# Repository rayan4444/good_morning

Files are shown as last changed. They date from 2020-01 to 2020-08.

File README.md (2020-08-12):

# Curtain scheduler

Scheduled curtain control: opens and closes at specific times

# Mechanical
### Assets
* Fusion 360 link: https://a360.co/35GVD2y
* See release for STEP/STL files

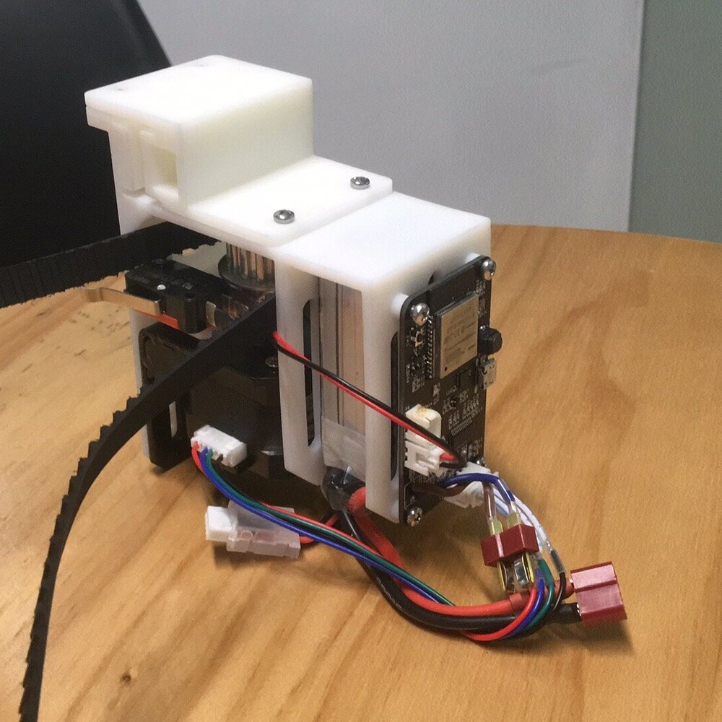
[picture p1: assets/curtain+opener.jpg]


### Improvements
* Add stiffness/ribs to reduce outer frame deflection
* smaller PCB mounting holes (changed diametr from 3mm to 2.7mm)
* larger chamfer to match curtain rail I have at home
* tighter tolerance on bearing holder
* choose a lighter/smaller motor bracket
* choos weaker/smaller mechanical end stops

# Electronics

### Description
Features:
* ESP32 WROOM32 module
* 1x button
* 1x programmable LED
* 1x VEML6030 ambient light sensor
* 1x CP2104 USB-UART bridge
* 1x DRV8825 stepper motor driver with controllable STEP, DIR, /SLEEP and /ENA

Power:
* 3S Lipo battery, charged externally - not by this board
* LDO for USB power during programming
* 12V-3.3V 1A switching regulator
* resistor divider to monitor battery voltage

>find out how long it lasts on 1 full charge

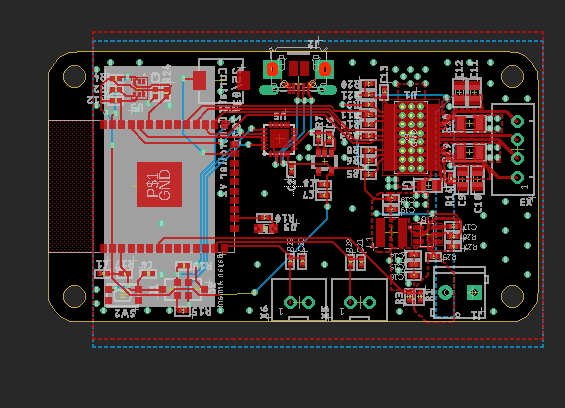
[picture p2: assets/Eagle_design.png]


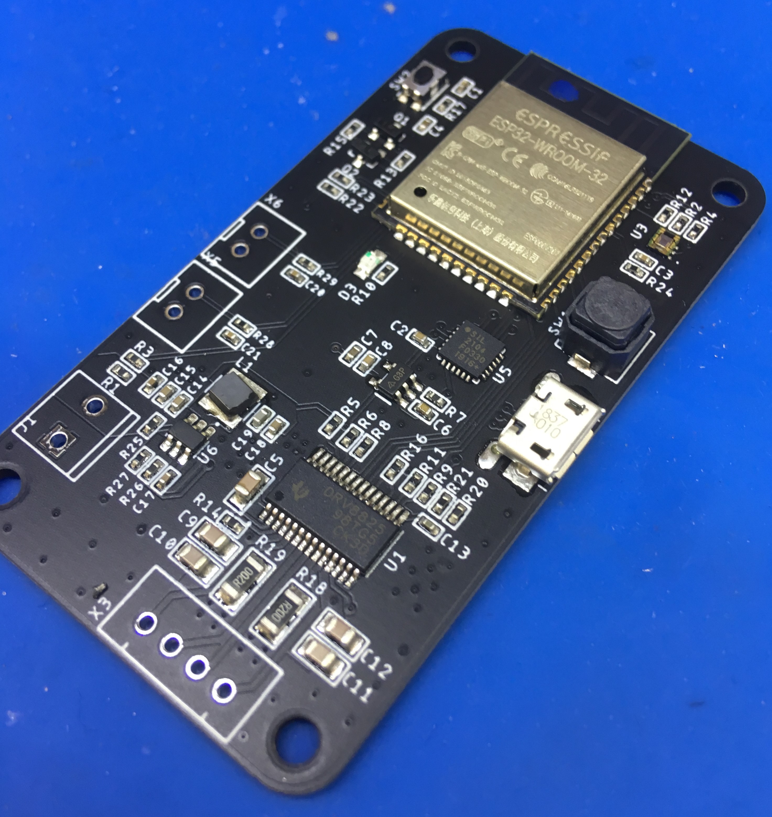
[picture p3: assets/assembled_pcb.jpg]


### Pinout
|Signal|Pin|Notes|
|:---:|:----:|:---:|
|Stepper_step|16||
|Stepper_direction|17||
|Stepper_enable|4|active low|
|Stepper_sleep|5|active low|
|Limit_switch_1|14|has external pullup (R23)|
|Limit_switch_2|12|no external pullup (R22), enable internal pullup|
|I2C_SCL|22||
|I2C_SDA|23||
|Ambient_light_sensor_int|21||
|LED|13||
|Button|15|enable internal pullup|
|Battery_voltage|I35, A1_7|ADC1 channel 7|

### Errata
* Remove R22: the external pullup messes with communication with flash when programming.
* Add 10k pull up resistor on the nENA line so that when the MCU is asleep the stepper is not enabled.

# Firmware

### Structure
* Wake up from sleep
* configure pins
* check battery level: if it is low blink the light and get stuck in this mode until the battery is recharged
* else, connect to wifi
* get time from NTP server
* check if it time to open/close the curtains
* open/close the curtains
* turn Wi-Fi OFF
* set wake up timer
* set wake up button
* go into deep sleep

> NOTE: this firmware version doesn't use the end stops to check the curtain status because the end stops I have are too strong and don't work. It will be updated once I find new end stops.

### Personal notes / improvements to do
* have a seperate RTC chip with less drift ?
* you can retain some simple things in RTC memory
```cpp
RTC_DATA_ATTR int bootCount = 0;
```
* change open/close times over wifi (from M5 stack core maybe?)
* "wireless wake up"?
* gather data from ambient light sensor over a week or so and see if there are any interesting patterns

### Reference links
* [deep sleep](https://lastminuteengineers.com/esp32-deep-sleep-wakeup-sources/)
* [NTP server](https://lastminuteengineers.com/esp32-ntp-server-date-time-tutorial/)
* [stepper driving with timers]()

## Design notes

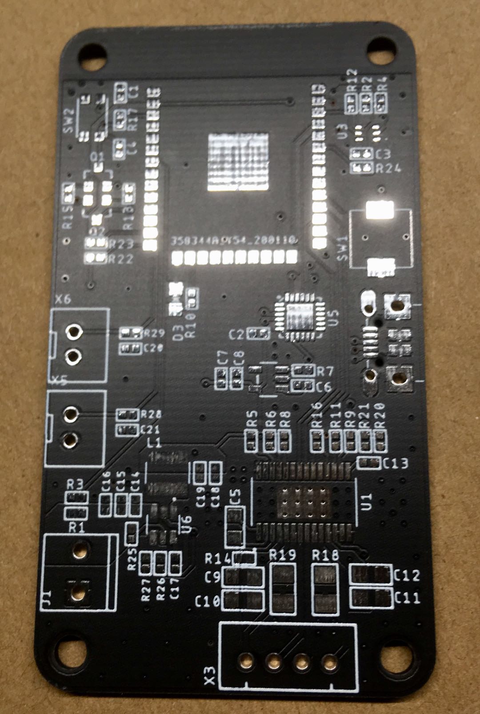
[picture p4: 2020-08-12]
assets/blank_pcb.jpg

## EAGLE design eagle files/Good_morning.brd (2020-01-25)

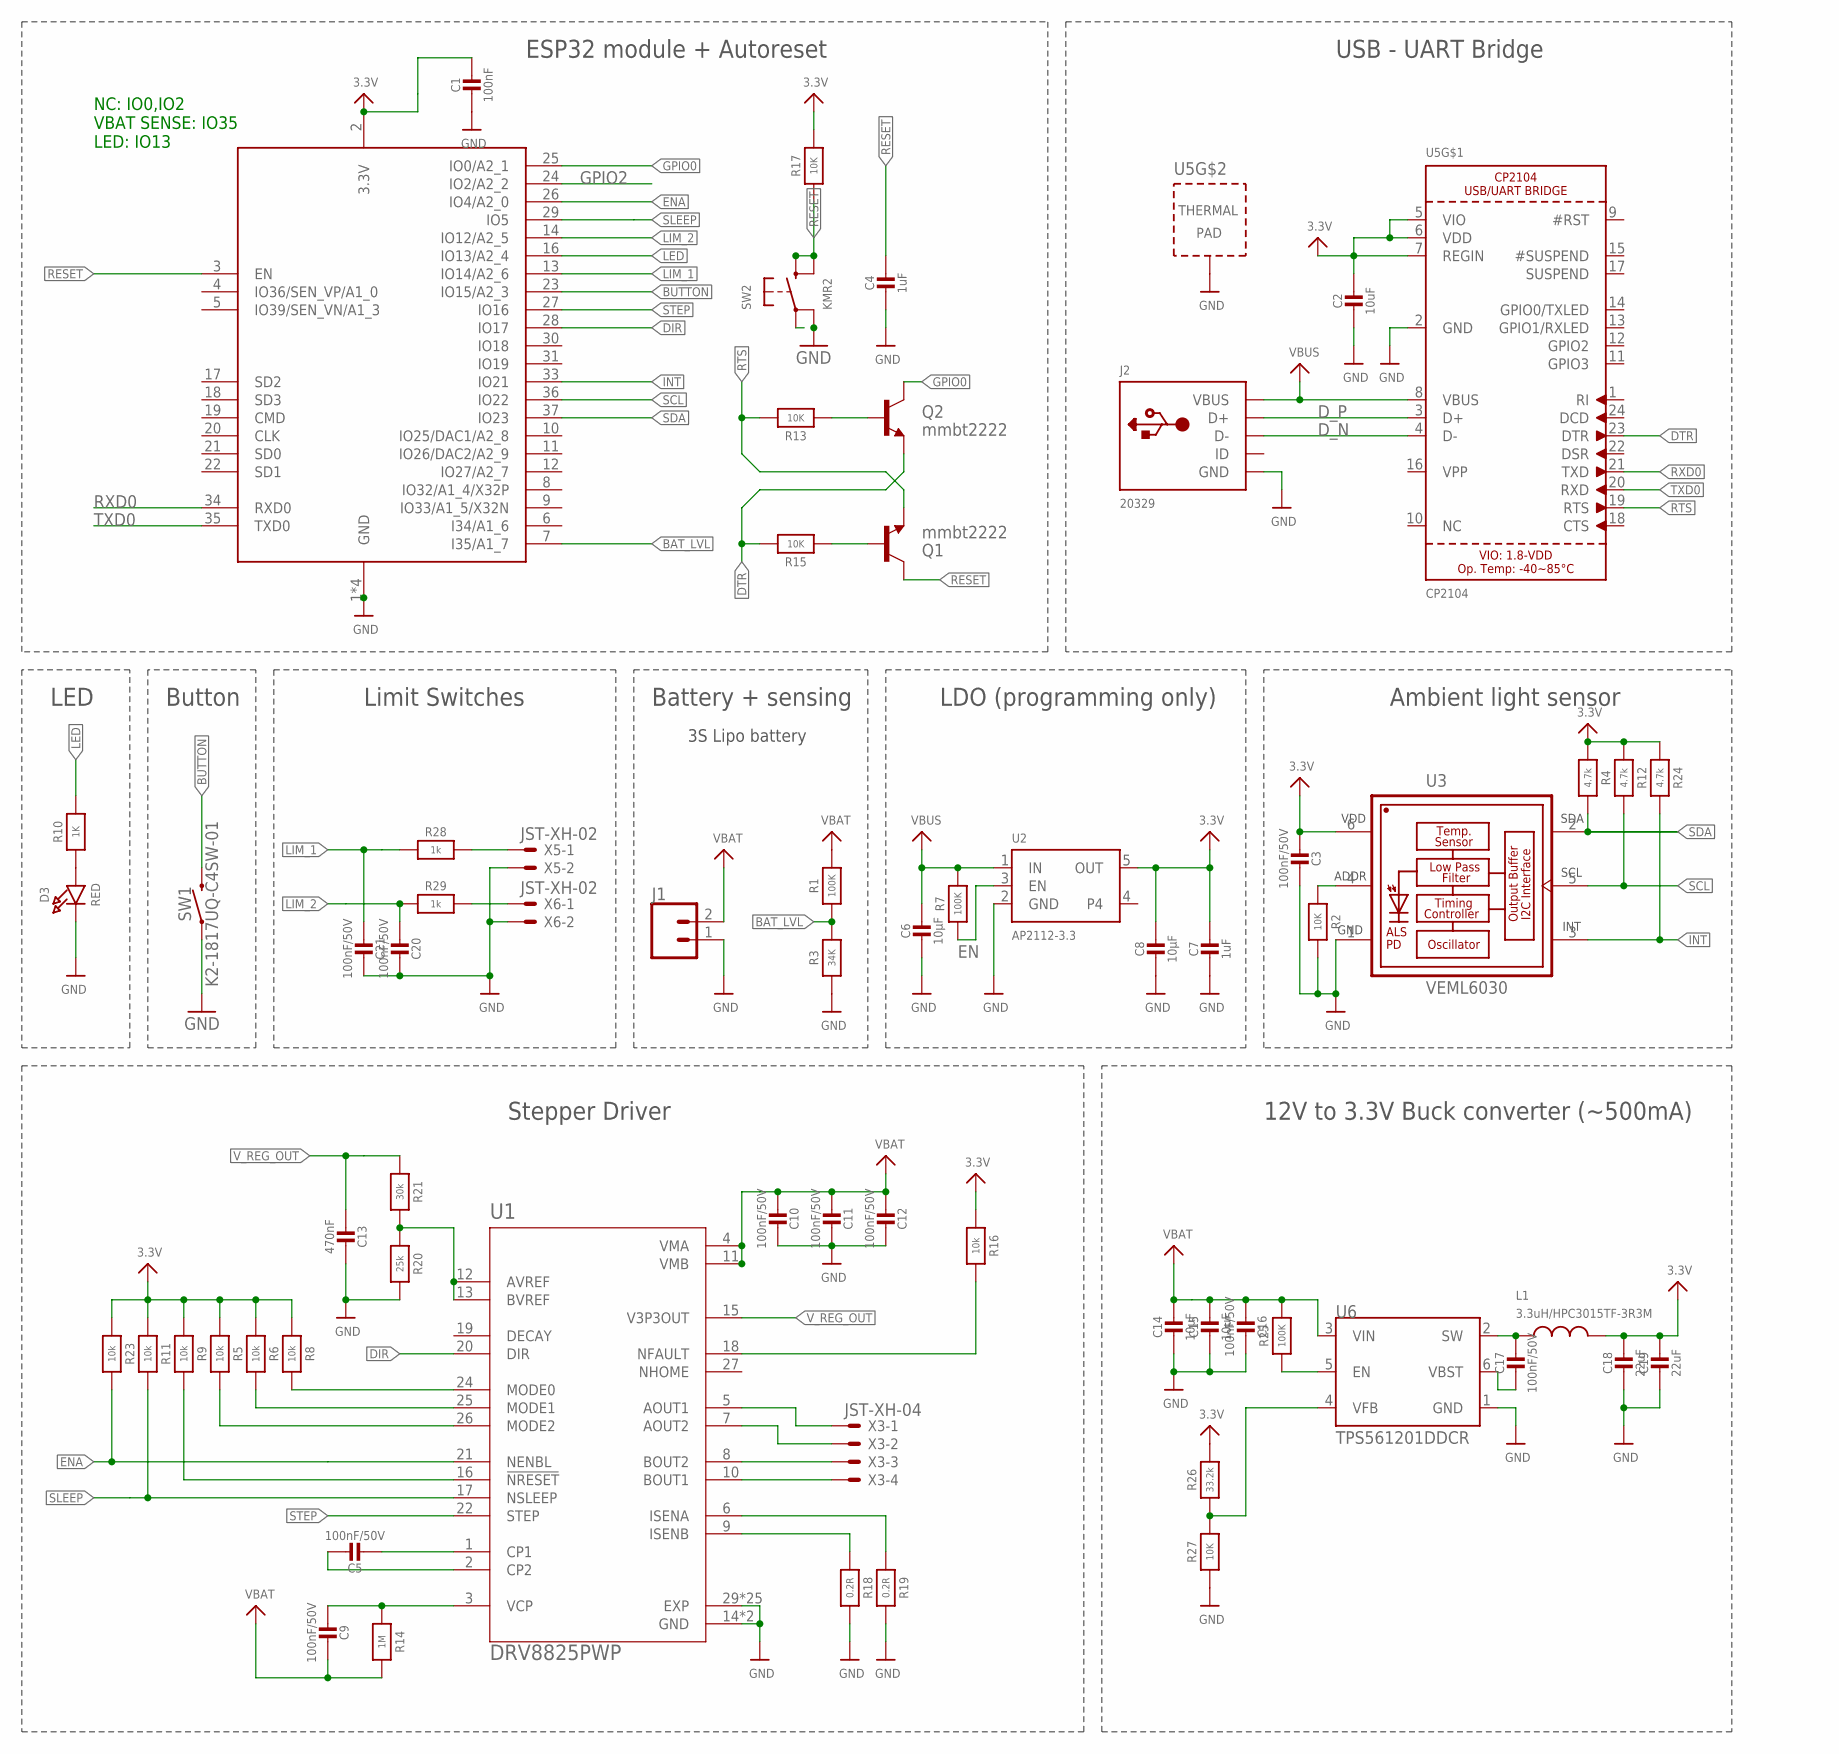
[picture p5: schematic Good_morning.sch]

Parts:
C1: 100nF; _0402
C2: 10uF; _0402
C3, C16, C17, C20, C21: 100nF/50V; _0402
C4, C7: 1uF; _0402
C5, C9, C10, C11, C12: 100nF/50V; _0805
C6, C8, C14, C15: 10µF; _0402
C13: 470nF; _0402
C18, C19: 22uF; _0402
D3: RED; CHIPLED_0805_NOOUTLINE
J1: CONN_023.5MM_LOCK; SCREWTERMINAL-3.5MM-2_LOCK
J2: 20329; 4UCONN_20329_V2
L1: 3.3uH/HPC3015TF-3R3M; WPN4020H100MT
Q1, Q2: mmbt2222; SOT23-3
R1, R7, R25: 100K; _0402
R2, R13, R15, R17, R27: 10K; _0402
R3: 34K; _0402
R4, R12, R24: 4.7k; _0402
R5, R6, R8, R9, R11, R16, R23: 10k; _0402
R10: 1K; _0402
R14: 1M; _0402
R18, R19: 0.2R; _1206
R20: 25k; _0402
R21: 30k; _0402
R26: 33.2k; _0402
R28, R29: 1k; _0402
SW1: K2-1817UQ-C4SW-01
SW2: KMR2; BTN_KMR2_4.6X2.8
U1: DRV8825PWP; SOP65P640X120-29N
U2: AP2112-3.3; SOT23-5
U3: VEML6030; VISHAY_VEML6030_2X2X0.87
U4: ESP32_WROOM32_SKINNY; WROOM32_SKINNY
U5: CP2104; QFN24_4MM_SMSC
U6: TPS561201DDCR; SOT95P280X110-6N
X3: JST-XH-04; JST-XH-04-PACKAGE-ROUND-PAD
X5, X6: JST-XH-02; JST-XH-02-PACKAGE-ROUND-PAD

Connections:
3.3V: C1.1, C2.1, C3.2, C7.1, C8.1, C18.1, C19.1, L1.2, R4.1, R5.1, R6.1, R8.1, R9.1, R11.1, R12.1, R16.1, R17.2, R23.1, R24.1, R26.1, U2.5 (OUT), U3.6 (VDD), U4.2 (3.3V), U5.5 (VIO), U5.6 (VDD), U5.7 (REGIN)
BAT_LVL: R1.1, R3.2, U4.7 (I35/A1_7)
BUTTON: SW1.P$2 (2), U4.23 (IO15/A2_3)
DIR: U1.20 (DIR), U4.28 (IO17)
DTR: Q2.2 (E), R15.2, U5.23 (DTR)
D_N: J2.D-, U5.4 (D-)
D_P: J2.D+, U5.3 (D+)
EN: R7.1, U2.3 (EN)
ENA: R23.2, U1.21 (NENBL), U4.26 (IO4/A2_0)
GND: C1.2, C2.2, C3.1, C4.2, C6.2, C7.2, C8.2, C10.1, C11.1, C12.1, C13.1, C14.2, C15.2, C16.1, C18.2, C19.2, C20.1, C21.1, D3.C, J1.1, J2.BASE@1 (GND), J2.BASE@2 (GND), J2.GND, J2.SPRT@1 (GND), J2.SPRT@2 (GND), J2.SPRT@3 (GND), J2.SPRT@4 (GND), R2.2, R3.1, R18.2, R19.2, R20.2, R27.1, SW1.P$1 (1), SW2.A' (P1), U1.14 (GND), U1.28 (GND), U1.29 (EXP), U1.P1 (EXP), U1.P2 (EXP), U1.P3 (EXP), U1.P4 (EXP), U1.P5 (EXP), U1.P6 (EXP), U1.P7 (EXP), U1.P8 (EXP), U1.P9 (EXP), U1.P10 (EXP), U1.P11 (EXP), U1.P12 (EXP), U1.P13 (EXP), U1.P14 (EXP), U1.P15 (EXP), U1.P16 (EXP), U1.P17 (EXP), U1.P18 (EXP), U1.P19 (EXP), U1.P20 (EXP), U1.P21 (EXP), U1.P22 (EXP), U1.P23 (EXP), U1.P24 (EXP), U2.2 (GND), U3.1 (GND), U4.1 (GND), U4.15 (GND), U4.38 (GND), U4.P$1 (GND), U5.2 (GND), U5.THERM (TP), U6.1 (GND), X5.2, X6.2
GPIO0: Q2.3 (C), U4.25 (IO0/A2_1)
GPIO2: U4.24 (IO2/A2_2)
INT: R24.2, U3.3 (INT), U4.33 (IO21)
LED: R10.1, U4.16 (IO13/A2_4)
LIM_1: C21.2, R28.1, U4.13 (IO14/A2_6)
LIM_2: C20.2, R29.1, U4.14 (IO12/A2_5)
unnamed: R2.1, U3.4 (ADDR)
unnamed: U1.8 (BOUT2), X3.3
unnamed: U1.10 (BOUT1), X3.4
unnamed: D3.A, R10.2
unnamed: R28.2, X5.1
unnamed: R25.1, U6.5 (EN)
unnamed: Q2.1 (B), R13.1
unnamed: R8.2, U1.24 (MODE0)
unnamed: R6.2, U1.25 (MODE1)
unnamed: R5.2, U1.26 (MODE2)
unnamed: Q1.1 (B), R15.1
unnamed: R9.2, U1.16 (!NRESET)
unnamed: C17.1, L1.1, U6.2 (SW)
unnamed: C5.2, U1.1 (CP1)
unnamed: C5.1, U1.2 (CP2)
unnamed: C9.2, R14.1, U1.3 (VCP)
unnamed: C17.2, U6.6 (VBST)
unnamed: R20.1, R21.2, U1.12 (AVREF), U1.13 (BVREF)
unnamed: R16.2, U1.18 (NFAULT)
unnamed: R29.2, X6.1
unnamed: U1.5 (AOUT1), X3.1
unnamed: U1.7 (AOUT2), X3.2
unnamed: R26.2, R27.2, U6.4 (VFB)
unnamed: R19.1, U1.6 (ISENA)
unnamed: R18.1, U1.9 (ISENB)
RESET: C4.1, Q1.3 (C), R17.1, SW2.B (S), SW2.B' (S1), U4.3 (EN)
RTS: Q1.2 (E), R13.2, U5.19 (RTS)
RXD0: U4.34 (RXD0), U5.21 (TXD)
SCL: R12.2, U3.5 (SCL), U4.36 (IO22)
SDA: R4.2, U3.2 (SDA), U4.37 (IO23)
SLEEP: R11.2, U1.17 (NSLEEP), U4.29 (IO5)
STEP: U1.22 (STEP), U4.27 (IO16)
TXD0: U4.35 (TXD0), U5.20 (RXD)
VBAT: C9.1, C10.2, C11.2, C12.2, C14.1, C15.1, C16.2, J1.2, R1.2, R14.2, R25.2, U1.4 (VMA), U1.11 (VMB), U6.3 (VIN)
VBUS: C6.1, J2.VBUS, R7.2, U2.1 (IN), U5.8 (VBUS)
V_REG_OUT: C13.2, R21.1, U1.15 (V3P3OUT)

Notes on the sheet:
NC: IO0,IO2 VBAT SENSE: IO35 LED: IO13
LDO (programming only)
Stepper Driver
LED
Button
ESP32 module + Autoreset
Battery + sensing
USB - UART Bridge
Limit Switches
3S Lipo battery
12V to 3.3V Buck converter (~500mA)
Ambient light sensor

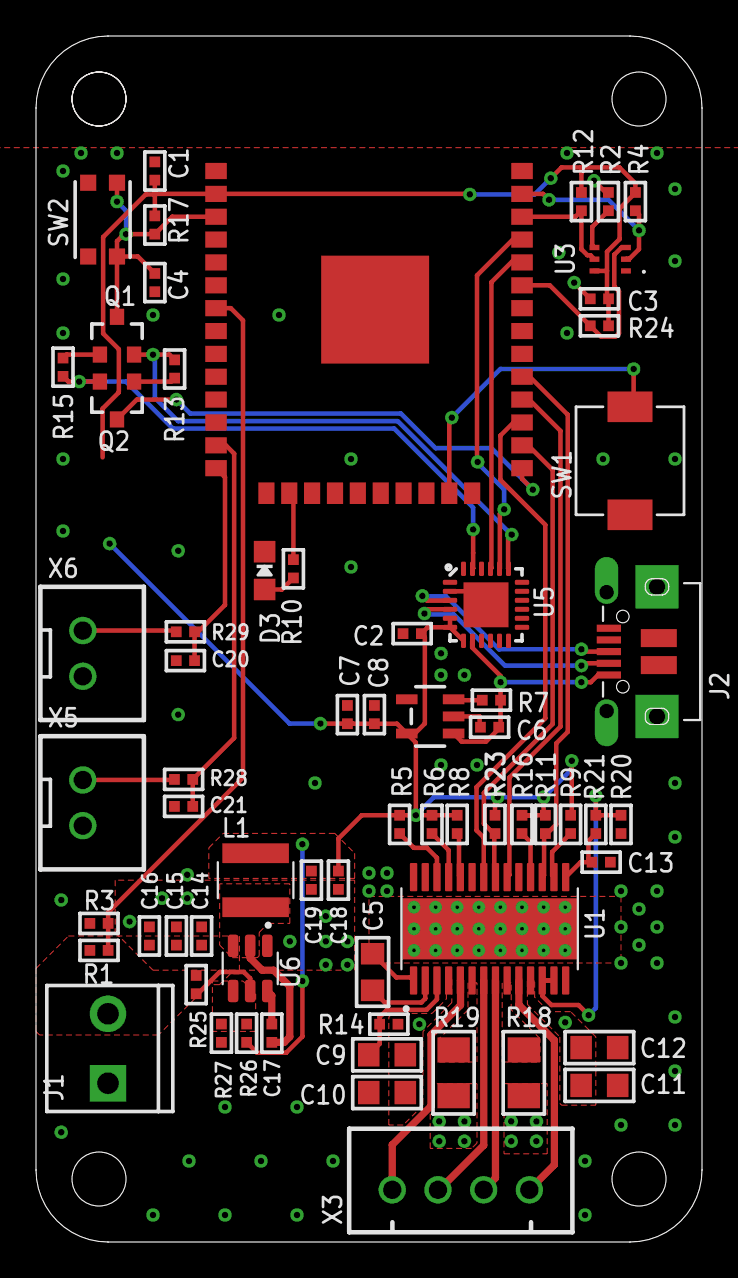
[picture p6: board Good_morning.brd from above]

Board: 2 copper layers, 37.0 x 67.0 mm, 66 parts (0 on the bottom side), 51 nets.

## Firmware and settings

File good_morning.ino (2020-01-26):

#include "Arduino.h"
#include <WiFi.h>

#define DEBUG

// time in between boot cycles
#define uS_TO_S_FACTOR 1000000 //Conversion factor for micro seconds to seconds
#define TIME_TO_SLEEP 30 //Time ESP32 will go to sleep (in seconds)

//math
const float pi = 3.14;

//pinout
#define led 13
#define step 16
#define dir 17
#define _ena 4
#define sleep 5
#define lim_1 14
#define lim_2 12
#define light_int 21
#define button 15 //also RTC_GPIO13
#define vbat 35

//flags
volatile bool button_pressed = 0;
volatile bool lim_1_reached = 0; //lim 1 reached means the curtain is fully open
volatile bool lim_2_reached = 0; //lim 2 reached means the curtain is fully closed
//WiFi credentials
const char* ssid = "XXX";
const char* password = "XXX";

//varialbles for time
const char* ntpServer = "pool.ntp.org";
const long gmtOffset_sec = 28800; //China is UTC+8 so offset: 8*3600 = 28800
const int daylightOffset_sec = 0; // China doesn't do Dailight saving so 0

//curtain open time
struct quand_t {
    int open_hour = 7;
    int open_min = 30;
    int open_late_hour = 10;
    int open_late_min = 30;
    int close_hour = 18;
    int close_min = 30;
} curtain;

//keeping the curtain status in memory during sleep
RTC_DATA_ATTR bool curtain_status = 0;

void setup()
{
    Serial.begin(115200);
    delay(1000);

    //print curtain status
    Serial.print("Curtain status: ");
    Serial.println(curtain_status);

    //check wake up reason
    print_wakeup_reason();

    //configure GPIO
    pinMode(led, OUTPUT);
    pinMode(step, OUTPUT);
    pinMode(dir, OUTPUT);
    pinMode(_ena, OUTPUT);
    pinMode(sleep, OUTPUT);
    pinMode(lim_1, INPUT);
    pinMode(lim_2, INPUT_PULLUP);
    pinMode(button, INPUT_PULLUP);
    pinMode(vbat, INPUT);

    //interrupts
    attachInterrupt(digitalPinToInterrupt(button), button_isr, FALLING);
    attachInterrupt(digitalPinToInterrupt(lim_1), lim_1_isr, FALLING);
    attachInterrupt(digitalPinToInterrupt(lim_2), lim_2_isr, FALLING);

    //setup stepper
    digitalWrite(_ena, HIGH);
    digitalWrite(sleep, HIGH);

    //if battery low, wake up every 5 seconds and blink the light but don't proceed
    if (vbat_low()){
        digitalWrite(led, HIGH);
        delay(1000);
        //Configure ESP wake up timer to 5s
        esp_sleep_enable_timer_wakeup(5 * uS_TO_S_FACTOR);
        //go back to sleep. the rest of the setup function will not run.
        esp_deep_sleep_start();
    }

    //connect to WiFi
    Serial.printf("Connecting to %s ", ssid);
    WiFi.begin(ssid, password);
    while (WiFi.status() != WL_CONNECTED) {
        Serial.print(".");
    }
    Serial.println(" CONNECTED");

    //init and get the time
    configTime(gmtOffset_sec, daylightOffset_sec, ntpServer);

    //handle the curtains
    curtaintime();

    //disconnect WiFi
    WiFi.disconnect(true);
    WiFi.mode(WIFI_OFF);

    //Configure ESP wake up timer to 5s
    esp_sleep_enable_timer_wakeup(TIME_TO_SLEEP * uS_TO_S_FACTOR);
    Serial.println("Setup ESP32 to sleep for every " + String(TIME_TO_SLEEP) + " Seconds");

    //Configure GPIO33 as ext0 wake up source for LOW logic level
    esp_sleep_enable_ext0_wakeup(GPIO_NUM_15, 0);

    //Go to sleep now
    esp_deep_sleep_start();
}

void loop()
{
}

void button_isr()
{
    // triggers when button is pressed
    button_pressed = 1;
    Serial.println("button pressed");
}

void lim_1_isr()
{
    //triggers when limit switch 1 is touched
    lim_1_reached = 1;
    Serial.println("limit swtch 1 pressed");
}

void lim_2_isr()
{
    //triggers when limit switch 2 is touched
    lim_2_reached = 1;
    Serial.println("limit swtch 2 pressed");
}

bool vbat_low()
{
    //true if the battery voltage is too low
    /* resistor divider 
    R1= 100k
    R2=34k
    (R2/(R1/R2))= 0.2537
    */

    int adc_raw = analogRead(vbat);
    float vref = 3.3;
    float voltage = vref * adc_raw;
    voltage = voltage / 4096.0;
    voltage = voltage / 0.237;

    // Serial.print("Battery voltage: ");
    // Serial.println(voltage);

    if (voltage < 9.0) {
        Serial.println("Battery low");
        return 1;
    } else {
        return 0;
    }
}

void curtaintime()
{
    struct tm timeinfo;
    if (!getLocalTime(&timeinfo)) {
        Serial.println("Failed to obtain time");
        return;
    }
    Serial.println(&timeinfo, "%A, %B %d %Y %H:%M:%S");
    int opening_hour, opening_min;
    // check opening time
    Serial.print("Day: ");
    Serial.println(timeinfo.tm_wday);
    if (timeinfo.tm_wday == 0) {
        opening_hour = curtain.open_late_hour;
        opening_min = curtain.open_late_min;
    } else {
        opening_hour = curtain.open_hour;
        opening_min = curtain.open_min;
    }
    //check if is time to open
    if (timeinfo.tm_hour == opening_hour) {
        //check minutes
        if (timeinfo.tm_min >= curtain.open_min) {
            
            if (!curtain_status){
            open_curtains();
            curtain_status=1;
            }else{
                Serial.println("curtain already open");
            }
        }
    }

    //check if it is time to close
    if (timeinfo.tm_hour == curtain.close_hour) {
        if (timeinfo.tm_min >= curtain.close_min) {
           if (curtain_status){
            close_curtains();
            curtain_status=0;           
           }
           else{
               Serial.println("curtain already closed");
           }
        }
    }
}


void open_curtains()
{
    Serial.println("curtains opening");
    move_stepper(-300); //move the stepper 20cm forward
}

void close_curtains()
{
    Serial.println("curtains closing");
    move_stepper(300); //move the stepper 20 cm back
}

void print_wakeup_reason()
{
    esp_sleep_wakeup_cause_t wakeup_reason;
    wakeup_reason = esp_sleep_get_wakeup_cause();
    switch (wakeup_reason) {
    case 1:
        Serial.println("Wakeup caused by external signal using RTC_IO");
        break;
    case 2:
        Serial.println("Wakeup caused by external signal using RTC_CNTL");
        break;
    case 3:
        Serial.println("Wakeup caused by timer");
        break;
    case 4:
        Serial.println("Wakeup caused by touchpad");
        break;
    case 5:
        Serial.println("Wakeup caused by ULP program");
        break;
    default:
        Serial.println("Wakeup was not caused by deep sleep");
        break;
    }
}

void move_stepper(int16_t distance) // distance in millimeters 
{
    // this will move the stepper in a direction for a set distance or until it hits an endstop

    // check direction
    if (distance < 0) {
        digitalWrite(dir, LOW);
        distance = -distance; // invert to keep positive math later
    } else {
        digitalWrite(dir, HIGH);
    }

    // enable stepper driver
    digitalWrite(_ena, LOW);
    digitalWrite(sleep, HIGH);

    // calculate step number
    //----------------------
    // 1 revolution = 360/1.8 = 200 steps
    // stepper driver is configured for 32 microsteps,1 revolution = 6400 microsteps.
    // diameter of timing belt gear: d = 25mm
    // 360 deg = 2*r*pi =>distance = d*pi*(deg/360) (mm)
    //distance = 25*pi*microsteps/6400
    // microsteps = distance *6400/(25*pi)
    uint32_t microsteps = (uint32_t)(6400 / (25 * pi));
    microsteps = distance * microsteps;

    for (int i = 0; i < microsteps; i++) {
        // check end stop flags
        if (lim_1_reached) {
            // disable the stepper
            digitalWrite(_ena, HIGH);
            digitalWrite(sleep, LOW);
            i = microsteps + 1; // exit the loop
            lim_1_reached=0;
            Serial.println("Stepper hit end stop");
        } else {
            // move by one microstep
            digitalWrite(step, HIGH);
            delayMicroseconds(50);
            digitalWrite(step, LOW);
            delayMicroseconds(50);
        }
    }
    Serial.println("Stepper done");
}

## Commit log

2020-01-10 Hardware files
    [Good_morning.brd, Good_morning.sch]
2020-01-16 tested sleep, ntp, bat, interrupts
2020-01-25 fixes mentioned in readme errata
    [Good_morning.brd, Good_morning.sch]

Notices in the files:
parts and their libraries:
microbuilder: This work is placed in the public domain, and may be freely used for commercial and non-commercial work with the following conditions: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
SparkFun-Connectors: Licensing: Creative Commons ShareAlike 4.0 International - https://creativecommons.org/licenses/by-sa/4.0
